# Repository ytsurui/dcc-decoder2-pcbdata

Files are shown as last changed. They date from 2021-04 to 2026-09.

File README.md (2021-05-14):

# ATtiny1606 DCC Decoder PCB Data

NMRA規格の信号を受信して動作する、DCCデコーダの基板設計データです。

主にNゲージ鉄道模型への搭載を想定して小型に設計しております。

## すべての基板に共通するスペック
  * 走行用モーター出力
  * BEMF読み取りによるフィードバック制御に対応
  * 最大7ファンクション出力
  * BiDi (Railcom) 出力
  * (試験的実装) Asymmetric DCCの認識回路
  
くわしくは、各基板のデータをご覧ください。
  * [K3066RA](docs/readme-K3066.md)
  * [K3057RA](docs/readme-K3057.md)
  * [M02F7RA Roomlight-N](docs/readme-roomlight-n.md)
  * [M02F7RA](docs/readme-normal.md)

## 閲覧・編集に必要なCAD (開発環境)
  * KiCad Version (5.1.9)-1 (またはそれ以降)

## 回路図

  * [v2021-04](https://github.com/ytsurui/dcc-decoder2-pcbdata/releases/tag/v2021-04)

## 対応するファームウェア
  * [ATtiny1606 DCC Decoder Firmware](https://github.com/ytsurui/dcc-decoder2-firmware)

このリポジトリに含まれる、すべての種類のデコーダが上記のファームウェアで動くように設計されています。

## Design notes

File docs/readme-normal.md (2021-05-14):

# ATtiny1606 DCC Decoder PCB Data (M02F7RA)

NMRA規格の信号を受信して動作する、DCCデコーダの基板設計データです。

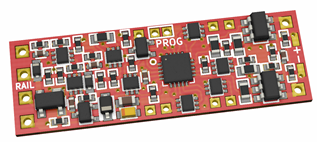
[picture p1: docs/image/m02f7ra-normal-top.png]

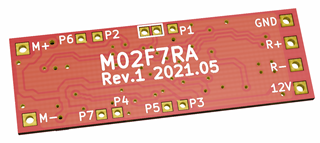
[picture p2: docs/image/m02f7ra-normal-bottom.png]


30mm x 10mmの汎用形状となっており、基板搭載スペースが確保可能な鉄道模型車両に搭載することができます。

  * [基板設計データ](../Normal/KiCad)
  
## 主要スペック
  * 組み立て後の基板サイズ： 30mm x 10mm x 1.7mm
  * 推奨最大電圧: 16V (搭載する鉄道模型車両の最大電圧以下で使用してください)
  * 出力電流: 最大0.5A (モーター) / 0.1A (ファンクション)
  * コンデンサの搭載や、室内灯電源に対応する+12V / GNDのランドを用意
  * マイコン書き込み用端子を用意し、実装後のプログラム書き換えも可能<br>UPDI 2pin Interface (GND / UPDI)

## 主な機能
  * モーター制御回路 (BEMF読み取り回路付き)
  * ファンクション出力 x 7<br>P1-P7すべてMOSFETによるドライブ、電流制限なし
  * BiDi (Railcom) 送出回路
  * (試験的実装) Asymmetric DCCの認識回路

## ファンクションの割り当て
<table>
  <tr>
    <td>基板上の番号</td>
    <td>ファンクションの推奨割り当て</td>
    <td>電気的特性</td>
  </tr>
  <tr>
    <td>P1</td>
    <td>ヘッドライト (前進)</td>
    <td>定電流出力 (約10mA)</td>
  </tr>
  <tr>
    <td>P2</td>
    <td>テールライト左 (後進/入替灯)</td>
    <td>定電流出力 (約1mA)</td>
  </tr>
  <tr>
    <td>P3</td>
    <td>テールライト右 (後進)</td>
    <td>定電流出力 (約1mA、スルーホール)<br>定電流出力 (約10mA、裏面パッド)</td>
  </tr>
  <tr>
    <td>P4</td>
    <td>ヘッドライト (後進)</td>
    <td>定電流出力 (約10mA)</td>
  </tr>
  <tr>
    <td>P5</td>
    <td>テールライト左 (前進/入替灯)</td>
    <td>定電流出力 (約1mA)</td>
  </tr>
  <tr>
    <td>P6</td>
    <td>テールライト右 (前進)</td>
    <td>定電流出力 (約1mA、スルーホール)<br>定電流出力 (約10mA、裏面パッド)</td>
  </tr>
  <tr>
    <td>P7</td>
    <td>キャブライト等、汎用ファンクション</td>
    <td>オープンドレイン (Max50mA程度)</td>
  </tr>
</table>

※番号表記はすべて基板の裏面にあります。

※ファンクションの推奨割り当ては対応するファームウェアでの初期状態を示しているものであり、ファームウェアを改修したり設定を変更すると変化する場合があります。

## 閲覧・編集に必要なCAD (開発環境)
  * KiCad Version (5.1.9)-1 (またはそれ以降)

### 対応するファームウェア
  * [ATtiny1606 DCC Decoder Firmware](https://github.com/ytsurui/dcc-decoder2-firmware)

### 各種ドキュメント
  * [パーツリスト](partslist-normal.md)

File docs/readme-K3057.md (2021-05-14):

# ATtiny1606 DCC Decoder PCB Data for KATO 3057 PCB Board

NMRA規格の信号を受信して動作する、DCCデコーダの基板設計データです。

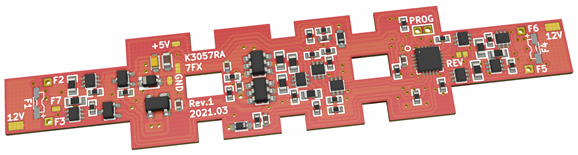
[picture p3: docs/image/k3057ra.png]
PCB 3D Preview


KATO製鉄道模型に搭載されている、3057と刻印のある基板と交換して取り付けができます。
<br>(その他、3010や3023など、形状が同等である他の刻印の基板との交換にも対応できる場合があります。)

  * [基板設計データ](../K3057/KiCad)
  * [面付けデータ](../K3057/KiCad-Panelized)
  * [ガーバーデータ(面付け済)](../K3057/Gerber-Panelized)
  * [メタルマスクデータ(面付け済)](../K3057/Stencil-Panelized)
  
面付け済みのデータについては、elecrowにて製造できることを確認済みです。

## 主要スペック
  * 組み立て後の基板サイズ： 69mm x 14mm x 1.7mm
  * 推奨最大電圧: 16V (搭載する鉄道模型車両の最大電圧以下で使用してください)
  * 出力電流: 最大0.5A (モーター) / 0.1A (ファンクション)
  * コンデンサの搭載や、室内灯電源に対応する+12V / GNDのランドを用意
  * マイコン書き込み用端子を用意し、実装後のプログラム書き換えも可能<br>UPDI 2pin Interface (GND / UPDI)

## 主な機能
  * モーター制御回路 (BEMF読み取り回路付き)
  * ファンクション出力 x 7<br>P1-P6は定電流出力、P7は電流制限なし
  * BiDi (Railcom) 送出回路
  * (試験的実装) Asymmetric DCCの認識回路

## ファンクションの割り当て
<table>
  <tr>
    <td>基板上の番号</td>
    <td>ファンクションの推奨割り当て</td>
    <td>電気的特性</td>
  </tr>
  <tr>
    <td>P1</td>
    <td>ヘッドライト (前進)</td>
    <td>定電流出力 (約10mA)</td>
  </tr>
  <tr>
    <td>P2</td>
    <td>テールライト左 (後進/入替灯)</td>
    <td>定電流出力 (約1mA)</td>
  </tr>
  <tr>
    <td>P3</td>
    <td>テールライト右 (後進)</td>
    <td>定電流出力 (約1mA、スルーホール)<br>定電流出力 (約10mA、裏面パッド)</td>
  </tr>
  <tr>
    <td>P4</td>
    <td>ヘッドライト (後進)</td>
    <td>定電流出力 (約10mA)</td>
  </tr>
  <tr>
    <td>P5</td>
    <td>テールライト左 (前進/入替灯)</td>
    <td>定電流出力 (約1mA)</td>
  </tr>
  <tr>
    <td>P6</td>
    <td>テールライト右 (前進)</td>
    <td>定電流出力 (約1mA、スルーホール)<br>定電流出力 (約10mA、裏面パッド)</td>
  </tr>
  <tr>
    <td>P7</td>
    <td>キャブライト等、汎用ファンクション</td>
    <td>オープンドレイン (Max50mA程度)</td>
  </tr>
</table>

※ファンクションの推奨割り当ては対応するファームウェアでの初期状態を示しているものであり、ファームウェアを改修したり設定を変更すると変化する場合があります。

## 閲覧・編集に必要なCAD (開発環境)
  * KiCad Version (5.1.9)-1 (またはそれ以降)

### 対応するファームウェア
  * [ATtiny1606 DCC Decoder Firmware](https://github.com/ytsurui/dcc-decoder2-firmware)

### 各種ドキュメント
  * [パーツリスト](partslist-K3057.md)

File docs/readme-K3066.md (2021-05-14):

# ATtiny1606 DCC Decoder PCB Data for KATO 3066 PCB Board

NMRA規格の信号を受信して動作する、DCCデコーダの基板設計データです。

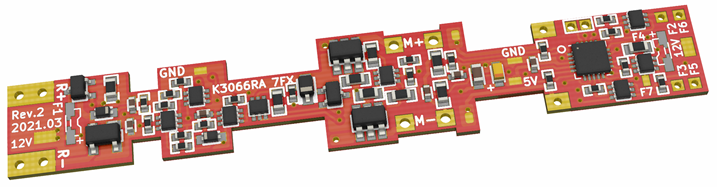
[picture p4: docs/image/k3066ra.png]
PCB 3D Preview


KATO製鉄道模型に搭載されている、3066と刻印のある基板と交換して取り付けができます。
<br>(その他、3070など、形状が同等である他の刻印の基板との交換にも対応できる場合があります。)

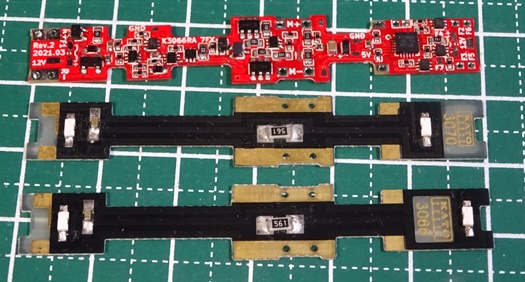
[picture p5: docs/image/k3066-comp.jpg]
PCB Compare


  * [基板設計データ](../K3066/KiCad)
  * [面付けデータ](../K3066/KiCad-Panelized)
  * [ガーバーデータ(面付け済)](../K3066/Gerber-Panelized)
  * [メタルマスクデータ(面付け済)](../K3066/Stencil-Panelized)
  
面付け済みのデータについては、elecrowにて製造できることを確認済みです。

## 主要スペック
  * 組み立て後の基板サイズ： 60mm x 10.5mm x 1.7mm
  * 推奨最大電圧: 16V (搭載する鉄道模型車両の最大電圧以下で使用してください)
  * 出力電流: 最大0.5A (モーター) / 0.1A (ファンクション)
  * コンデンサの搭載や、室内灯電源に対応する+12V / GNDのランドを用意
  * マイコン書き込み用端子を用意し、実装後のプログラム書き換えも可能<br>UPDI 2pin Interface (GND / UPDI)

## 主な機能
  * モーター制御回路 (BEMF読み取り回路付き)
  * ファンクション出力 x 7<br>P1-P6は定電流出力、P7は電流制限なし
  * BiDi (Railcom) 送出回路
  * (試験的実装) Asymmetric DCCの認識回路

## ファンクションの割り当て
<table>
  <tr>
    <td>基板上の番号</td>
    <td>ファンクションの推奨割り当て</td>
    <td>電気的特性</td>
  </tr>
  <tr>
    <td>P1</td>
    <td>ヘッドライト (前進)</td>
    <td>定電流出力 (約10mA)</td>
  </tr>
  <tr>
    <td>P2</td>
    <td>テールライト左 (後進/入替灯)</td>
    <td>定電流出力 (約1mA)</td>
  </tr>
  <tr>
    <td>P3</td>
    <td>テールライト右 (後進)</td>
    <td>定電流出力 (約1mA)</td>
  </tr>
  <tr>
    <td>P4</td>
    <td>ヘッドライト (後進)</td>
    <td>定電流出力 (約10mA)</td>
  </tr>
  <tr>
    <td>P5</td>
    <td>テールライト左 (前進/入替灯)</td>
    <td>定電流出力 (約1mA)</td>
  </tr>
  <tr>
    <td>P6</td>
    <td>テールライト右 (前進)</td>
    <td>定電流出力 (約1mA)</td>
  </tr>
  <tr>
    <td>P7</td>
    <td>キャブライト等、汎用ファンクション</td>
    <td>オープンドレイン (Max50mA程度)</td>
  </tr>
</table>

※ファンクションの推奨割り当ては対応するファームウェアでの初期状態を示しているものであり、ファームウェアを改修したり設定を変更すると変化する場合があります。

## 閲覧・編集に必要なCAD (開発環境)
  * KiCad Version (5.1.9)-1 (またはそれ以降)

## 対応するファームウェア
  * [ATtiny1606 DCC Decoder Firmware](https://github.com/ytsurui/dcc-decoder2-firmware)

## 各種ドキュメント
  * [パーツリスト](partslist-K3066.md)

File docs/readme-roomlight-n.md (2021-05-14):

# ATtiny1606 DCC Decoder PCB Data for Roomlight (Narrow Type)

NMRA規格の信号を受信して動作する、DCCデコーダの基板設計データです。

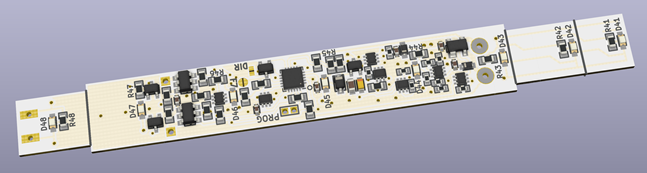
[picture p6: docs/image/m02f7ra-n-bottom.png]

PCB 3D Preview

TOMIX製やマイクロエース製の室内灯に近い形としており、室内灯一体型デコーダとしての利用が可能です。

  * [基板設計データ](../RoomLightNarrow/KiCad)
  * [面付けデータ](../RoomLightNarrow/KiCad-Panelized)
  * [ガーバーデータ(面付け済)](../RoomLightNarrow/Gerber-Panelized)
  * [メタルマスクデータ(面付け済)](../RoomLightNarrow/Stencil-Panelized)
  
面付け済みのデータについては、elecrowにて製造できることを確認済みです。

## 主要スペック
  * 組み立て後の基板サイズ： 87mm x 10mm x 1.7mm
  * 推奨最大電圧: 16V (搭載する鉄道模型車両の最大電圧以下で使用してください)
  * 出力電流: 最大0.5A (モーター) / 0.1A (ファンクション)
  * コンデンサの搭載や、室内灯電源に対応する+12V / GNDのランドを用意
  * マイコン書き込み用端子を用意し、実装後のプログラム書き換えも可能<br>UPDI 2pin Interface (GND / UPDI)

## 主な機能
  * モーター制御回路 (BEMF読み取り回路付き)
  * ファンクション出力 x 7<br>P1-P6はパッドで用意、P7は室内灯LED駆動回路に直結<br>※すべてのパッドで電流制限回路なし
  * BiDi (Railcom) 送出回路
  * (試験的実装) Asymmetric DCCの認識回路

## ファンクションの割り当て
<table>
  <tr>
    <td>基板上の番号</td>
    <td>ファンクションの推奨割り当て</td>
    <td>電気的特性</td>
  </tr>
  <tr>
    <td>P1</td>
    <td>ヘッドライト (前進)</td>
    <td>オープンドレイン (Max50mA程度)</td>
  </tr>
  <tr>
    <td>P2</td>
    <td>テールライト左 (後進/入替灯)</td>
    <td>オープンドレイン (Max50mA程度)</td>
  </tr>
  <tr>
    <td>P3</td>
    <td>テールライト右 (後進)</td>
    <td>オープンドレイン (Max50mA程度)</td>
  </tr>
  <tr>
    <td>P4</td>
    <td>ヘッドライト (後進)</td>
    <td>オープンドレイン (Max50mA程度)</td>
  </tr>
  <tr>
    <td>P5</td>
    <td>テールライト左 (前進/入替灯)</td>
    <td>オープンドレイン (Max50mA程度)</td>
  </tr>
  <tr>
    <td>P6</td>
    <td>テールライト右 (前進)</td>
    <td>オープンドレイン (Max50mA程度)</td>
  </tr>
  <tr>
    <td>P7</td>
    <td>キャブライト等、汎用ファンクション</td>
    <td>室内灯回路直結 (Max50mA程度)</td>
  </tr>
  <tr>
    <td>MOTOR+ / MOTOR-<br>(モータードライバ)</td>
    <td>ヘッドライト / テールライト<br>(ライト基板を無改造で接続)</td>
    <td>Hブリッジ出力</td>
  </tr>
</table>

モータードライバをファンクションとして利用するためには、CV値を書き換える必要がある場合があります。
<br>また、走行用モーター出力とは排他利用となります。

※ファンクションの推奨割り当ては対応するファームウェアでの初期状態を示しているものであり、ファームウェアを改修したり設定を変更すると変化する場合があります。

## 閲覧・編集に必要なCAD (開発環境)
  * KiCad Version (5.1.9)-1 (またはそれ以降)

### 対応するファームウェア
  * [ATtiny1606 DCC Decoder Firmware](https://github.com/ytsurui/dcc-decoder2-firmware)

### 各種ドキュメント
  * [パーツリスト](partslist-RoomlightNarrow.md)

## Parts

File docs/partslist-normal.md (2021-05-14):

# Parts List (MotorDecoder2-Normal, Rev1)

<table>
  <th>
    <td>Name</td>
    <td>Package</td>
    <td>Count</td>
    <td>Shop Links</td>
  </th>
  <tr>
    <td>U2</td>
    <td>ATtiny1606-MNR</td>
    <td>VQFN-20 (3x3mm)</td>
    <td>1</td>
    <td><a href="https://www.digikey.jp/product-detail/ja/microchip-technology/ATTINY1606-MNR/150-ATTINY1606-MNRCT-ND/11476321">Digikey (ja)</a></td>
  </tr>
  <tr>
    <td>D1</td>
    <td>BAS3007A-RPP</td>
    <td>SOT-143</td>
    <td>1</td>
    <td><a href="https://www.digikey.jp/product-detail/ja/infineon-technologies/BAS3007ARPPE6327HTSA1/BAS3007ARPPE6327HTSA1CT-ND/2023144">Digikey (ja)</a><br />
    <a href="https://www.digikey.jp/product-detail/en/infineon-technologies/BAS3007ARPPE6327HTSA1/BAS3007ARPPE6327HTSA1CT-ND/2023144">Digikey (en)</a></td>
  </tr>
  <tr>
    <td>D3</td>
    <td>UDZV5.6B</td>
    <td>SOD-323</td>
    <td>1</td>
    <td><a href="https://www.digikey.jp/product-detail/ja/rohm-semiconductor/UDZVTE-175-1B/UDZVTE-175-1BCT-ND/4571455">Digikey (ja)</a><br />
    <a href="https://www.digikey.jp/product-detail/en/rohm-semiconductor/UDZVTE-175-1B/UDZVTE-175-1BCT-ND/4571455">Digikey (en)</a></td>
  </tr>
  <tr>
    <td>D11, D12</td>
    <td>LED</td>
    <td></td>
    <td>2</td>
    <td></td>
  </tr>
  <tr>
    <td>D21, D22</td>
    <td>BAT43XV2</td>
    <td></td>
    <td>2</td>
    <td></td>
  </tr>
  <tr>
    <td>Q1, Q2</td>
    <td>DMG6601LVT<br>DMG6602SVTQ<br>FDC6333</td>
    <td>SOT-23-6</td>
    <td>2</td>
    <td><a href="https://www.digikey.jp/product-detail/ja/diodes-incorporated/DMG6601LVT-7/DMG6601LVT-7DICT-ND/3677910">Digikey, DMG6601LVT (ja)</a><br />
    <a href="https://www.digikey.jp/product-detail/en/diodes-incorporated/DMG6601LVT-7/DMG6601LVT-7DICT-ND/3677910">Digikey, DMG6601LVT (en)</a><br>
    <a href="https://www.digikey.jp/product-detail/ja/diodes-incorporated/DMG6602SVTQ-7/DMG6602SVTQ-7DICT-ND/5176059">Digikey, DMG6602SVTQ (ja)</a><br>
    <a href="https://www.digikey.jp/product-detail/en/diodes-incorporated/DMG6602SVTQ-7/DMG6602SVTQ-7DICT-ND/5176059">Digikey, DMG6602SVTQ (en)</a><br>
    <a href="https://www.digikey.jp/product-detail/ja/on-semiconductor/FDC6333C/FDC6333CCT-ND/965584">Digikey, FDC6333 (ja)</a><br>
    <a href="https://www.digikey.jp/product-detail/en/on-semiconductor/FDC6333C/FDC6333CCT-ND/965584">Digikey, FDC6333 (en)</a>
    </td>
  </tr>
  <tr>
    <td>Q3, Q8</td>
    <td>PMBT3904VS,115</td>
    <td>SOT-666</td>
    <td>2</td>
    <td><a href="https://www.digikey.jp/product-detail/ja/nexperia-usa-inc/PMBT3904VS,115/1727-5177-1-ND/2531775">Digikey (ja)</a></td>
  </tr>
  <tr>
    <td>Q5</td>
    <td>2SC4116-GR</td>
    <td>SC-70</td>
    <td>1</td>
    <td><a href="https://www.digikey.jp/product-detail/ja/toshiba-semiconductor-and-storage/2SC4116-GR-LF/2SC4116-GRLFCT-ND/3191333">Digikey (ja)</a><br />
    <a href="https://www.digikey.jp/product-detail/en/toshiba-semiconductor-and-storage/2SC4116-GR-LF/2SC4116-GRLFCT-ND/3191333">Digikey (en)</a><br />
    <a href="https://akizukidenshi.com/catalog/g/gI-02705/">秋月電子通商</a></td>
  </tr>
  <tr>
    <td>Q6, Q21</td>
    <td>PMBT3906VS,115</td>
    <td>SOT-666</td>
    <td>2</td>
    <td><a href="https://www.digikey.jp/product-detail/ja/nexperia-usa-inc/PMBT3906VS,115/1727-5179-1-ND/2531777">Digikey (ja)</a></td>
  </tr>
  <tr>
    <td>Q12-Q14, Q22</td>
    <td>SSM6N7002BFE</td>
    <td>SOT-666</td>
    <td>5</td>
    <td><a href="https://www.digikey.jp/product-detail/ja/toshiba-semiconductor-and-storage/SSM6N7002BFE,LM/SSM6N7002BFELMCT-ND/4880063">Digikey (ja)</a></td>
  </tr>
  <tr>
    <td>Q11</td>
    <td>SSM3K7002BFU<br>SSM3K7002KFU</td>
    <td>SC-70</td>
    <td>1</td>
    <td><a href="https://www.digikey.jp/product-detail/ja/toshiba-semiconductor-and-storage/SSM3K7002KFU-LF/SSM3K7002KFULFCT-ND/8543465">Digikey (ja)</a><br><a href="https://akizukidenshi.com/catalog/g/gI-08576/">秋月電子通商</a></td>
  </tr>
  <tr>
    <td>C1, C5</td>
	  <td>0.1uF 25V 1005</td>
	  <td>1.0mm x 0.5mm</td>
	  <td>2</td>
    <td><a href="https://www.digikey.jp/product-detail/ja/murata-electronics/GRM155R71H104KE14J/490-13342-1-ND/5973352">Digikey (ja)</a><br />
    <a href="https://www.digikey.jp/product-detail/en/murata-electronics/GRM155R71H104KE14J/490-13342-1-ND/5973352">Digikey (en)</a><br />
    <a href="https://akizukidenshi.com/catalog/g/gP-13377/">秋月電子通商</a></td>
  </tr>
  <tr>
    <td>C3</td>
    <td>22uF 6.3V 1608</td>
    <td>1.6mm x 0.8mm</td>
    <td>1</td>
    <td><a href="https://www.digikey.jp/product-detail/ja/murata-electronics/GRM188R60J226MEA0D/490-7611-1-ND/4280544">Digikey (ja)</a><br />
    <a href="https://www.digikey.jp/product-detail/en/murata-electronics/GRM188R60J226MEA0D/490-7611-1-ND/4280544">Digikey (en)</a><br />
    <a href="https://akizukidenshi.com/catalog/g/gP-08062/">秋月電子通商</a></td>
  </tr>
  <tr>
    <td>C4</td>
    <td>47uF 6.3V 1608 Tantalum</td>
    <td>1.6mm x 0.8mm</td>
    <td>1</td>
    <td><a href="https://www.digikey.jp/product-detail/ja/rohm-semiconductor/TCSOM0J476M8R-ZM1/511-11830-1-ND/10258991">Digikey (ja)</a></td>
  </tr>
  <tr>
    <td>C7</td>
    <td>1800pF 50V 1005</td>
    <td>1.0x0.5mm</td>
    <td>1</td>
    <td><a href="https://akizukidenshi.com/catalog/g/gP-15443/">秋月電子通商</a></td>
  </tr>
  <tr>
    <td>C11, C12</td>
	<td>1.0uF 25V 1005</td>
	<td>1.0mm x 0.5mm</td>
	<td>2</td>
    <td><a href="https://www.digikey.jp/product-detail/ja/murata-electronics/GRM155R71H104KE14J/490-13342-1-ND/5973352">Digikey (ja)</a><br />
    <a href="https://www.digikey.jp/product-detail/en/murata-electronics/GRM155R71H104KE14J/490-13342-1-ND/5973352">Digikey (en)</a><br />
    <a href="https://akizukidenshi.com/catalog/g/gP-13377/">秋月電子通商</a></td>
  </tr>
  <tr>
    <td>R1, R2, R17, R18</td>
    <td>100kohm 1/16W 1005</td>
    <td>1.0x0.5mm</td>
    <td>4</td>
    <td><a href="https://www.digikey.jp/product-detail/ja/bourns-inc/CR0402-FX-1003GLF/CR0402-FX-1003GLFCT-ND/3740841">Digikey (ja)</a></td>
  </tr>
  <tr>
    <td>R3, R4</td>
    <td>1kohm 1/10W 1608</td>
    <td>1.6x0.8mm</td>
    <td>2</td>
    <td><a href="https://www.digikey.jp/products/ja/resistors/chip-resistor-surface-mount/52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">Digikey (ja)</a><br />
    <a href="https://www.digikey.jp/products/en/resistors/chip-resistor-surface-mount/52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">Digikey (en)</a><br />
    <a href="https://akizukidenshi.com/catalog/g/gR-14122/">秋月電子通商</a></td>
  </tr>
  <tr>
    <td>R5, R6</td>
    <td>330ohm 1/10W 1608</td>
    <td>1.6x0.8mm</td>
    <td>2</td>
    <td><a href="https://www.digikey.jp/products/ja/resistors/chip-resistor-surface-mount/52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">Digikey (ja)</a><br />
    <a href="https://www.digikey.jp/products/en/resistors/chip-resistor-surface-mount/52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">Digikey (en)</a><br />
    <a href="https://akizukidenshi.com/catalog/g/gR-06331/">秋月電子通商</a></td>
  </tr>
  <tr>
    <td>R7, R8, R11, R31, R35</td>
    <td>1kohm 1/16W 1005</td>
    <td>1.0x0.5mm</td>
    <td>5</td>
    <td><a href="https://www.digikey.jp/products/ja/resistors/chip-resistor-surface-mount/52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">Digikey (ja)</a></td>
  </tr>
  <tr>
    <td>R12, R33, R37</td>
    <td>4.7kohm 1/16W 1005</td>
    <td>1.0x0.5mm</td>
    <td>3</td>
    <td><a href="https://www.digikey.jp/product-detail/ja/koa-speer-electronics-inc/RK73B1ETTP472J/2019-RK73B1ETTP472JCT-ND/9846006">Digikey (ja)</a></td>
  </tr>
  <tr>
    <td>R9, R10, R13, R16, R32, R34, R36, R38</td>
    <td>10kohm 1/16W 1005</td>
    <td>1.0x0.5mm</td>
    <td>8</td>
    <td><a href="https://www.digikey.jp/product-detail/ja/koa-speer-electronics-inc/RK73B1ETTP103J/2019-RK73B1ETTP103JCT-ND/9846004">Digikey (ja)</a></td>
  </tr>
  <tr>
    <td>R14</td>
    <td>22ohm 1/10W 1608</td>
    <td>1.6x0.8mm</td>
    <td>1</td>
    <td><a href="https://www.digikey.jp/product-detail/ja/koa-speer-electronics-inc/RK73B1JTTD220J/2019-RK73B1JTTD220JCT-ND/9846752">Digikey (ja)</a></td>
  </tr>
  <tr>
    <td>R15</td>
    <td>6.8kohm 1/16W 1005</td>
    <td>1.0x0.5mm</td>
    <td>1</td>
    <td><a href="https://www.digikey.jp/product-detail/ja/koa-speer-electronics-inc/RK73B1ETTP682J/2019-RK73B1ETTP682JCT-ND/9846058">Digikey (ja)</a></td>
  </tr>

</table>

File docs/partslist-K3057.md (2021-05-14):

# Parts List (MotorDecoder2-K3057, Rev2)

<table>
  <th>
    <td>Name</td>
    <td>Package</td>
    <td>Count</td>
    <td>Shop Links</td>
  </th>
  <tr>
    <td>U2</td>
    <td>ATtiny1606-MNR</td>
    <td>VQFN-20 (3x3mm)</td>
    <td>1</td>
    <td><a href="https://www.digikey.jp/product-detail/ja/microchip-technology/ATTINY1606-MNR/150-ATTINY1606-MNRCT-ND/11476321">Digikey (ja)</a></td>
  </tr>
  <tr>
    <td>D1</td>
    <td>BAS3007A-RPP</td>
    <td>SOT-143</td>
    <td>1</td>
    <td><a href="https://www.digikey.jp/product-detail/ja/infineon-technologies/BAS3007ARPPE6327HTSA1/BAS3007ARPPE6327HTSA1CT-ND/2023144">Digikey (ja)</a><br />
    <a href="https://www.digikey.jp/product-detail/en/infineon-technologies/BAS3007ARPPE6327HTSA1/BAS3007ARPPE6327HTSA1CT-ND/2023144">Digikey (en)</a></td>
  </tr>
  <tr>
    <td>D3</td>
    <td>UDZV5.6B</td>
    <td>SOD-323</td>
    <td>1</td>
    <td><a href="https://www.digikey.jp/product-detail/ja/rohm-semiconductor/UDZVTE-175-1B/UDZVTE-175-1BCT-ND/4571455">Digikey (ja)</a><br />
    <a href="https://www.digikey.jp/product-detail/en/rohm-semiconductor/UDZVTE-175-1B/UDZVTE-175-1BCT-ND/4571455">Digikey (en)</a></td>
  </tr>
  <tr>
    <td>D11, D12</td>
    <td>LED</td>
    <td></td>
    <td>2</td>
    <td></td>
  </tr>
  <tr>
    <td>D21, D22</td>
    <td>BAT43XV2</td>
    <td></td>
    <td>2</td>
    <td></td>
  </tr>
  <tr>
    <td>Q1, Q2</td>
    <td>DMG6601LVT<br>DMG6602SVTQ<br>FDC6333</td>
    <td>SOT-23-6</td>
    <td>2</td>
    <td><a href="https://www.digikey.jp/product-detail/ja/diodes-incorporated/DMG6601LVT-7/DMG6601LVT-7DICT-ND/3677910">Digikey, DMG6601LVT (ja)</a><br />
    <a href="https://www.digikey.jp/product-detail/en/diodes-incorporated/DMG6601LVT-7/DMG6601LVT-7DICT-ND/3677910">Digikey, DMG6601LVT (en)</a><br>
    <a href="https://www.digikey.jp/product-detail/ja/diodes-incorporated/DMG6602SVTQ-7/DMG6602SVTQ-7DICT-ND/5176059">Digikey, DMG6602SVTQ (ja)</a><br>
    <a href="https://www.digikey.jp/product-detail/en/diodes-incorporated/DMG6602SVTQ-7/DMG6602SVTQ-7DICT-ND/5176059">Digikey, DMG6602SVTQ (en)</a><br>
    <a href="https://www.digikey.jp/product-detail/ja/on-semiconductor/FDC6333C/FDC6333CCT-ND/965584">Digikey, FDC6333 (ja)</a><br>
    <a href="https://www.digikey.jp/product-detail/en/on-semiconductor/FDC6333C/FDC6333CCT-ND/965584">Digikey, FDC6333 (en)</a>
    </td>
  </tr>
  <tr>
    <td>Q3, Q8</td>
    <td>PMBT3904VS,115</td>
    <td>SOT-666</td>
    <td>2</td>
    <td><a href="https://www.digikey.jp/product-detail/ja/nexperia-usa-inc/PMBT3904VS,115/1727-5177-1-ND/2531775">Digikey (ja)</a></td>
  </tr>
  <tr>
    <td>Q5</td>
    <td>2SC4116-GR</td>
    <td>SC-70</td>
    <td>1</td>
    <td><a href="https://www.digikey.jp/product-detail/ja/toshiba-semiconductor-and-storage/2SC4116-GR-LF/2SC4116-GRLFCT-ND/3191333">Digikey (ja)</a><br />
    <a href="https://www.digikey.jp/product-detail/en/toshiba-semiconductor-and-storage/2SC4116-GR-LF/2SC4116-GRLFCT-ND/3191333">Digikey (en)</a><br />
    <a href="https://akizukidenshi.com/catalog/g/gI-02705/">秋月電子通商</a></td>
  </tr>
  <tr>
    <td>Q6, Q21</td>
    <td>PMBT3906VS,115</td>
    <td>SOT-666</td>
    <td>2</td>
    <td><a href="https://www.digikey.jp/product-detail/ja/nexperia-usa-inc/PMBT3906VS,115/1727-5179-1-ND/2531777">Digikey (ja)</a></td>
  </tr>
  <tr>
    <td>Q11-Q14, Q22</td>
    <td>SSM6N7002BFE</td>
    <td>SOT-666</td>
    <td>5</td>
    <td><a href="https://www.digikey.jp/product-detail/ja/toshiba-semiconductor-and-storage/SSM6N7002BFE,LM/SSM6N7002BFELMCT-ND/4880063">Digikey (ja)</a></td>
  </tr>
  <tr>
    <td>Q15</td>
    <td>SSM3K7002BFU<br>SSM3K7002KFU</td>
    <td>SC-70</td>
    <td>1</td>
    <td><a href="https://www.digikey.jp/product-detail/ja/toshiba-semiconductor-and-storage/SSM3K7002KFU-LF/SSM3K7002KFULFCT-ND/8543465">Digikey (ja)</a><br><a href="https://akizukidenshi.com/catalog/g/gI-08576/">秋月電子通商</a></td>
  </tr>
  <tr>
    <td>C1, C5</td>
	  <td>0.1uF 25V 1005</td>
	  <td>1.0mm x 0.5mm</td>
	  <td>2</td>
    <td><a href="https://www.digikey.jp/product-detail/ja/murata-electronics/GRM155R71H104KE14J/490-13342-1-ND/5973352">Digikey (ja)</a><br />
    <a href="https://www.digikey.jp/product-detail/en/murata-electronics/GRM155R71H104KE14J/490-13342-1-ND/5973352">Digikey (en)</a><br />
    <a href="https://akizukidenshi.com/catalog/g/gP-13377/">秋月電子通商</a></td>
  </tr>
  <tr>
    <td>C3</td>
    <td>22uF 6.3V 1608</td>
    <td>1.6mm x 0.8mm</td>
    <td>1</td>
    <td><a href="https://www.digikey.jp/product-detail/ja/murata-electronics/GRM188R60J226MEA0D/490-7611-1-ND/4280544">Digikey (ja)</a><br />
    <a href="https://www.digikey.jp/product-detail/en/murata-electronics/GRM188R60J226MEA0D/490-7611-1-ND/4280544">Digikey (en)</a><br />
    <a href="https://akizukidenshi.com/catalog/g/gP-08062/">秋月電子通商</a></td>
  </tr>
  <tr>
    <td>C4</td>
    <td>47uF 6.3V 1608 Tantalum</td>
    <td>1.6mm x 0.8mm</td>
    <td>1</td>
    <td><a href="https://www.digikey.jp/product-detail/ja/rohm-semiconductor/TCSOM0J476M8R-ZM1/511-11830-1-ND/10258991">Digikey (ja)</a></td>
  </tr>
  <tr>
    <td>C7</td>
    <td>1800pF 50V 1005</td>
    <td>1.0x0.5mm</td>
    <td>1</td>
    <td><a href="https://akizukidenshi.com/catalog/g/gP-15443/">秋月電子通商</a></td>
  </tr>
  <tr>
    <td>C11, C12</td>
	<td>1.0uF 25V 1005</td>
	<td>1.0mm x 0.5mm</td>
	<td>2</td>
    <td><a href="https://www.digikey.jp/product-detail/ja/murata-electronics/GRM155R71H104KE14J/490-13342-1-ND/5973352">Digikey (ja)</a><br />
    <a href="https://www.digikey.jp/product-detail/en/murata-electronics/GRM155R71H104KE14J/490-13342-1-ND/5973352">Digikey (en)</a><br />
    <a href="https://akizukidenshi.com/catalog/g/gP-13377/">秋月電子通商</a></td>
  </tr>
  <tr>
    <td>R1, R2, R17, R18</td>
    <td>100kohm 1/16W 1005</td>
    <td>1.0x0.5mm</td>
    <td>4</td>
    <td><a href="https://www.digikey.jp/product-detail/ja/bourns-inc/CR0402-FX-1003GLF/CR0402-FX-1003GLFCT-ND/3740841">Digikey (ja)</a></td>
  </tr>
  <tr>
    <td>R3, R4</td>
    <td>1kohm 1/10W 1608</td>
    <td>1.6x0.8mm</td>
    <td>2</td>
    <td><a href="https://www.digikey.jp/products/ja/resistors/chip-resistor-surface-mount/52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">Digikey (ja)</a><br />
    <a href="https://www.digikey.jp/products/en/resistors/chip-resistor-surface-mount/52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">Digikey (en)</a><br />
    <a href="https://akizukidenshi.com/catalog/g/gR-14122/">秋月電子通商</a></td>
  </tr>
  <tr>
    <td>R5, R6</td>
    <td>330ohm 1/10W 1608</td>
    <td>1.6x0.8mm</td>
    <td>2</td>
    <td><a href="https://www.digikey.jp/products/ja/resistors/chip-resistor-surface-mount/52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">Digikey (ja)</a><br />
    <a href="https://www.digikey.jp/products/en/resistors/chip-resistor-surface-mount/52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">Digikey (en)</a><br />
    <a href="https://akizukidenshi.com/catalog/g/gR-06331/">秋月電子通商</a></td>
  </tr>
  <tr>
    <td>R7, R8, R11, R31, R35</td>
    <td>1kohm 1/16W 1005</td>
    <td>1.0x0.5mm</td>
    <td>5</td>
    <td><a href="https://www.digikey.jp/products/ja/resistors/chip-resistor-surface-mount/52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">Digikey (ja)</a></td>
  </tr>
  <tr>
    <td>R9, R10</td>
    <td>10kohm 1/10W 1608</td>
    <td>1.6mm x 0.8mm</td>
    <td>2</td>
    <td><a href="https://www.digikey.jp/products/ja/resistors/chip-resistor-surface-mount/52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">Digikey (ja)</a><br />
    <a href="https://www.digikey.jp/products/en/resistors/chip-resistor-surface-mount/52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">Digikey (en)</a><br />
    <a href="https://akizukidenshi.com/catalog/g/gR-06103/">秋月電子通商</a></td>
  </tr>
  <tr>
    <td>R12, R23-R26, R33, R37</td>
    <td>4.7kohm 1/16W 1005</td>
    <td>1.0x0.5mm</td>
    <td>7</td>
    <td><a href="https://www.digikey.jp/product-detail/ja/koa-speer-electronics-inc/RK73B1ETTP472J/2019-RK73B1ETTP472JCT-ND/9846006">Digikey (ja)</a></td>
  </tr>
  <tr>
    <td>R13, R16, R32, R34, R36, R38</td>
    <td>10kohm 1/16W 1005</td>
    <td>1.0x0.5mm</td>
    <td>5</td>
    <td><a href="https://www.digikey.jp/product-detail/ja/koa-speer-electronics-inc/RK73B1ETTP103J/2019-RK73B1ETTP103JCT-ND/9846004">Digikey (ja)</a></td>
  </tr>
  <tr>
    <td>R14</td>
    <td>22ohm 1/10W 1608</td>
    <td>1.6x0.8mm</td>
    <td>1</td>
    <td><a href="https://www.digikey.jp/product-detail/ja/koa-speer-electronics-inc/RK73B1JTTD220J/2019-RK73B1JTTD220JCT-ND/9846752">Digikey (ja)</a></td>
  </tr>
  <tr>
    <td>R15</td>
    <td>6.8kohm 1/16W 1005</td>
    <td>1.0x0.5mm</td>
    <td>1</td>
    <td><a href="https://www.digikey.jp/product-detail/ja/koa-speer-electronics-inc/RK73B1ETTP682J/2019-RK73B1ETTP682JCT-ND/9846058">Digikey (ja)</a></td>
  </tr>
  <tr>
    <td>R21, R22, R27, R28</td>
    <td>150ohm 1/10W 1608</td>
    <td>1.6x0.8mm</td>
    <td>2</td>
    <td><a href="https://www.digikey.jp/products/ja/resistors/chip-resistor-surface-mount/52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">Digikey (ja)</a></td>
  </tr>

</table>

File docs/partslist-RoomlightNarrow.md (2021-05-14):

# Parts List (MotorDecoder2-Roomlight-Narrow, Rev2)

<table>
  <th>
    <td>Name</td>
    <td>Package</td>
    <td>Count</td>
    <td>Shop Links</td>
  </th>
  <tr>
    <td>U2</td>
    <td>ATtiny1606-MNR</td>
    <td>VQFN-20 (3x3mm)</td>
    <td>1</td>
    <td><a href="https://www.digikey.jp/product-detail/ja/microchip-technology/ATTINY1606-MNR/150-ATTINY1606-MNRCT-ND/11476321">Digikey (ja)</a></td>
  </tr>
  <tr>
    <td>D1</td>
    <td>BAS3007A-RPP</td>
    <td>SOT-143</td>
    <td>1</td>
    <td><a href="https://www.digikey.jp/product-detail/ja/infineon-technologies/BAS3007ARPPE6327HTSA1/BAS3007ARPPE6327HTSA1CT-ND/2023144">Digikey (ja)</a><br />
    <a href="https://www.digikey.jp/product-detail/en/infineon-technologies/BAS3007ARPPE6327HTSA1/BAS3007ARPPE6327HTSA1CT-ND/2023144">Digikey (en)</a></td>
  </tr>
  <tr>
    <td>D3</td>
    <td>UDZV5.6B</td>
    <td>SOD-323</td>
    <td>1</td>
    <td><a href="https://www.digikey.jp/product-detail/ja/rohm-semiconductor/UDZVTE-175-1B/UDZVTE-175-1BCT-ND/4571455">Digikey (ja)</a><br />
    <a href="https://www.digikey.jp/product-detail/en/rohm-semiconductor/UDZVTE-175-1B/UDZVTE-175-1BCT-ND/4571455">Digikey (en)</a></td>
  </tr>
  <tr>
    <td>D41-D48</td>
    <td>LED 1608サイズ<br>(室内灯用)</td>
    <td>1.6mmx0.8mm</td>
    <td>8</td>
    <td>-</td>
  </tr>
  <tr>
    <td>D21, D22</td>
    <td>BAT43XV2</td>
    <td></td>
    <td>2</td>
    <td></td>
  </tr>
  <tr>
    <td>Q1, Q2</td>
    <td>DMG6601LVT<br>DMG6602SVTQ<br>FDC6333</td>
    <td>SOT-23-6</td>
    <td>2</td>
    <td><a href="https://www.digikey.jp/product-detail/ja/diodes-incorporated/DMG6601LVT-7/DMG6601LVT-7DICT-ND/3677910">Digikey, DMG6601LVT (ja)</a><br />
    <a href="https://www.digikey.jp/product-detail/en/diodes-incorporated/DMG6601LVT-7/DMG6601LVT-7DICT-ND/3677910">Digikey, DMG6601LVT (en)</a><br>
    <a href="https://www.digikey.jp/product-detail/ja/diodes-incorporated/DMG6602SVTQ-7/DMG6602SVTQ-7DICT-ND/5176059">Digikey, DMG6602SVTQ (ja)</a><br>
    <a href="https://www.digikey.jp/product-detail/en/diodes-incorporated/DMG6602SVTQ-7/DMG6602SVTQ-7DICT-ND/5176059">Digikey, DMG6602SVTQ (en)</a><br>
    <a href="https://www.digikey.jp/product-detail/ja/on-semiconductor/FDC6333C/FDC6333CCT-ND/965584">Digikey, FDC6333 (ja)</a><br>
    <a href="https://www.digikey.jp/product-detail/en/on-semiconductor/FDC6333C/FDC6333CCT-ND/965584">Digikey, FDC6333 (en)</a>
    </td>
  </tr>
  <tr>
    <td>Q3, Q8</td>
    <td>PMBT3904VS,115</td>
    <td>SOT-666</td>
    <td>2</td>
    <td><a href="https://www.digikey.jp/product-detail/ja/nexperia-usa-inc/PMBT3904VS,115/1727-5177-1-ND/2531775">Digikey (ja)</a></td>
  </tr>
  <tr>
    <td>Q5</td>
    <td>2SC4116-GR</td>
    <td>SC-70</td>
    <td>1</td>
    <td><a href="https://www.digikey.jp/product-detail/ja/toshiba-semiconductor-and-storage/2SC4116-GR-LF/2SC4116-GRLFCT-ND/3191333">Digikey (ja)</a><br />
    <a href="https://www.digikey.jp/product-detail/en/toshiba-semiconductor-and-storage/2SC4116-GR-LF/2SC4116-GRLFCT-ND/3191333">Digikey (en)</a><br />
    <a href="https://akizukidenshi.com/catalog/g/gI-02705/">秋月電子通商</a></td>
  </tr>
  <tr>
    <td>Q6, Q21</td>
    <td>PMBT3906VS,115</td>
    <td>SOT-666</td>
    <td>2</td>
    <td><a href="https://www.digikey.jp/product-detail/ja/nexperia-usa-inc/PMBT3906VS,115/1727-5179-1-ND/2531777">Digikey (ja)</a></td>
  </tr>
  <tr>
    <td>Q13, Q14, Q22</td>
    <td>SSM6N7002BFE</td>
    <td>SOT-666</td>
    <td>3</td>
    <td><a href="https://www.digikey.jp/product-detail/ja/toshiba-semiconductor-and-storage/SSM6N7002BFE,LM/SSM6N7002BFELMCT-ND/4880063">Digikey (ja)</a></td>
  </tr>
  <tr>
    <td>Q11, Q12, Q17</td>
    <td>SSM3K7002BFU<br>SSM3K7002KFU</td>
    <td>SC-70</td>
    <td>3</td>
    <td><a href="https://www.digikey.jp/product-detail/ja/toshiba-semiconductor-and-storage/SSM3K7002KFU-LF/SSM3K7002KFULFCT-ND/8543465">Digikey (ja)</a><br><a href="https://akizukidenshi.com/catalog/g/gI-08576/">秋月電子通商</a></td>
  </tr>
  <tr>
    <td>C1, C5</td>
	  <td>0.1uF 25V 1005</td>
	  <td>1.0mm x 0.5mm</td>
	  <td>2</td>
    <td><a href="https://www.digikey.jp/product-detail/ja/murata-electronics/GRM155R71H104KE14J/490-13342-1-ND/5973352">Digikey (ja)</a><br />
    <a href="https://www.digikey.jp/product-detail/en/murata-electronics/GRM155R71H104KE14J/490-13342-1-ND/5973352">Digikey (en)</a><br />
    <a href="https://akizukidenshi.com/catalog/g/gP-13377/">秋月電子通商</a></td>
  </tr>
  <tr>
    <td>C3</td>
    <td>22uF 6.3V 1608</td>
    <td>1.6mm x 0.8mm</td>
    <td>1</td>
    <td><a href="https://www.digikey.jp/product-detail/ja/murata-electronics/GRM188R60J226MEA0D/490-7611-1-ND/4280544">Digikey (ja)</a><br />
    <a href="https://www.digikey.jp/product-detail/en/murata-electronics/GRM188R60J226MEA0D/490-7611-1-ND/4280544">Digikey (en)</a><br />
    <a href="https://akizukidenshi.com/catalog/g/gP-08062/">秋月電子通商</a></td>
  </tr>
  <tr>
    <td>C4</td>
    <td>47uF 6.3V 1608 Tantalum</td>
    <td>1.6mm x 0.8mm</td>
    <td>1</td>
    <td><a href="https://www.digikey.jp/product-detail/ja/rohm-semiconductor/TCSOM0J476M8R-ZM1/511-11830-1-ND/10258991">Digikey (ja)</a></td>
  </tr>
  <tr>
    <td>C7</td>
    <td>1800pF 50V 1005</td>
    <td>1.0x0.5mm</td>
    <td>1</td>
    <td><a href="https://akizukidenshi.com/catalog/g/gP-15443/">秋月電子通商</a></td>
  </tr>
  <tr>
    <td>C11, C12</td>
	<td>1.0uF 25V 1005</td>
	<td>1.0mm x 0.5mm</td>
	<td>2</td>
    <td><a href="https://www.digikey.jp/product-detail/ja/murata-electronics/GRM155R71H104KE14J/490-13342-1-ND/5973352">Digikey (ja)</a><br />
    <a href="https://www.digikey.jp/product-detail/en/murata-electronics/GRM155R71H104KE14J/490-13342-1-ND/5973352">Digikey (en)</a><br />
    <a href="https://akizukidenshi.com/catalog/g/gP-13377/">秋月電子通商</a></td>
  </tr>
  <tr>
    <td>R1, R2, R17</td>
    <td>100kohm 1/10W 1608</td>
    <td>1.6x0.8mm</td>
    <td>3</td>
    <td><a href="https://www.digikey.jp/products/ja/resistors/chip-resistor-surface-mount/52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">Digikey (ja)</a><br />
    <a href="https://www.digikey.jp/products/en/resistors/chip-resistor-surface-mount/52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">Digikey (en)</a><br />
    <a href="https://akizukidenshi.com/catalog/g/gR-15321/">秋月電子通商</a></td>
  </tr>
  <tr>
    <td>R18</td>
    <td>100kohm 1/16W 1005</td>
    <td>1.0x0.5mm</td>
    <td>1</td>
    <td><a href="https://www.digikey.jp/product-detail/ja/bourns-inc/CR0402-FX-1003GLF/CR0402-FX-1003GLFCT-ND/3740841">Digikey (ja)</a></td>
  </tr>
  <tr>
    <td>R3, R4</td>
    <td>1kohm 1/10W 1608</td>
    <td>1.6x0.8mm</td>
    <td>2</td>
    <td><a href="https://www.digikey.jp/products/ja/resistors/chip-resistor-surface-mount/52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">Digikey (ja)</a><br />
    <a href="https://www.digikey.jp/products/en/resistors/chip-resistor-surface-mount/52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">Digikey (en)</a><br />
    <a href="https://akizukidenshi.com/catalog/g/gR-14122/">秋月電子通商</a></td>
  </tr>
  <tr>
    <td>R5, R6</td>
    <td>330ohm 1/10W 1608</td>
    <td>1.6x0.8mm</td>
    <td>2</td>
    <td><a href="https://www.digikey.jp/products/ja/resistors/chip-resistor-surface-mount/52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">Digikey (ja)</a><br />
    <a href="https://www.digikey.jp/products/en/resistors/chip-resistor-surface-mount/52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">Digikey (en)</a><br />
    <a href="https://akizukidenshi.com/catalog/g/gR-06331/">秋月電子通商</a></td>
  </tr>
  <tr>
    <td>R7, R8, R11, R31, R35</td>
    <td>1kohm 1/16W 1005</td>
    <td>1.0x0.5mm</td>
    <td>5</td>
    <td><a href="https://www.digikey.jp/products/ja/resistors/chip-resistor-surface-mount/52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">Digikey (ja)</a></td>
  </tr>
  <tr>
    <td>R9, R10</td>
    <td>10kohm 1/10W 1608</td>
    <td>1.6mm x 0.8mm</td>
    <td>2</td>
    <td><a href="https://www.digikey.jp/products/ja/resistors/chip-resistor-surface-mount/52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">Digikey (ja)</a><br />
    <a href="https://www.digikey.jp/products/en/resistors/chip-resistor-surface-mount/52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">Digikey (en)</a><br />
    <a href="https://akizukidenshi.com/catalog/g/gR-06103/">秋月電子通商</a></td>
  </tr>
  <tr>
    <td>R12<br>R41-R48</td>
    <td>4.7kohm 1/10W 1608</td>
    <td>1.6mm x 0.8mm</td>
    <td>9</td>
    <td><a href="https://www.digikey.jp/products/ja/resistors/chip-resistor-surface-mount/52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">Digikey (ja)</a><br />
    <a href="https://www.digikey.jp/products/en/resistors/chip-resistor-surface-mount/52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">Digikey (en)</a><br />
    <a href="https://akizukidenshi.com/catalog/g/gR-14121/">秋月電子通商</a></td>
  </tr>
  <tr>
    <td>R33, R37</td>
    <td>4.7kohm 1/16W 1005</td>
    <td>1.0x0.5mm</td>
    <td>2</td>
    <td><a href="https://www.digikey.jp/product-detail/ja/koa-speer-electronics-inc/RK73B1ETTP472J/2019-RK73B1ETTP472JCT-ND/9846006">Digikey (ja)</a></td>
  </tr>
  <tr>
    <td>R13, R16, R32, R34, R36, R38</td>
    <td>10kohm 1/16W 1005</td>
    <td>1.0x0.5mm</td>
    <td>5</td>
    <td><a href="https://www.digikey.jp/product-detail/ja/koa-speer-electronics-inc/RK73B1ETTP103J/2019-RK73B1ETTP103JCT-ND/9846004">Digikey (ja)</a></td>
  </tr>
  <tr>
    <td>R14</td>
    <td>22ohm 1/10W 1608</td>
    <td>1.6x0.8mm</td>
    <td>1</td>
    <td><a href="https://www.digikey.jp/product-detail/ja/koa-speer-electronics-inc/RK73B1JTTD220J/2019-RK73B1JTTD220JCT-ND/9846752">Digikey (ja)</a></td>
  </tr>
  <tr>
    <td>R15</td>
    <td>6.8kohm 1/16W 1005</td>
    <td>1.0x0.5mm</td>
    <td>1</td>
    <td><a href="https://www.digikey.jp/product-detail/ja/koa-speer-electronics-inc/RK73B1ETTP682J/2019-RK73B1ETTP682JCT-ND/9846058">Digikey (ja)</a></td>
  </tr>

</table>

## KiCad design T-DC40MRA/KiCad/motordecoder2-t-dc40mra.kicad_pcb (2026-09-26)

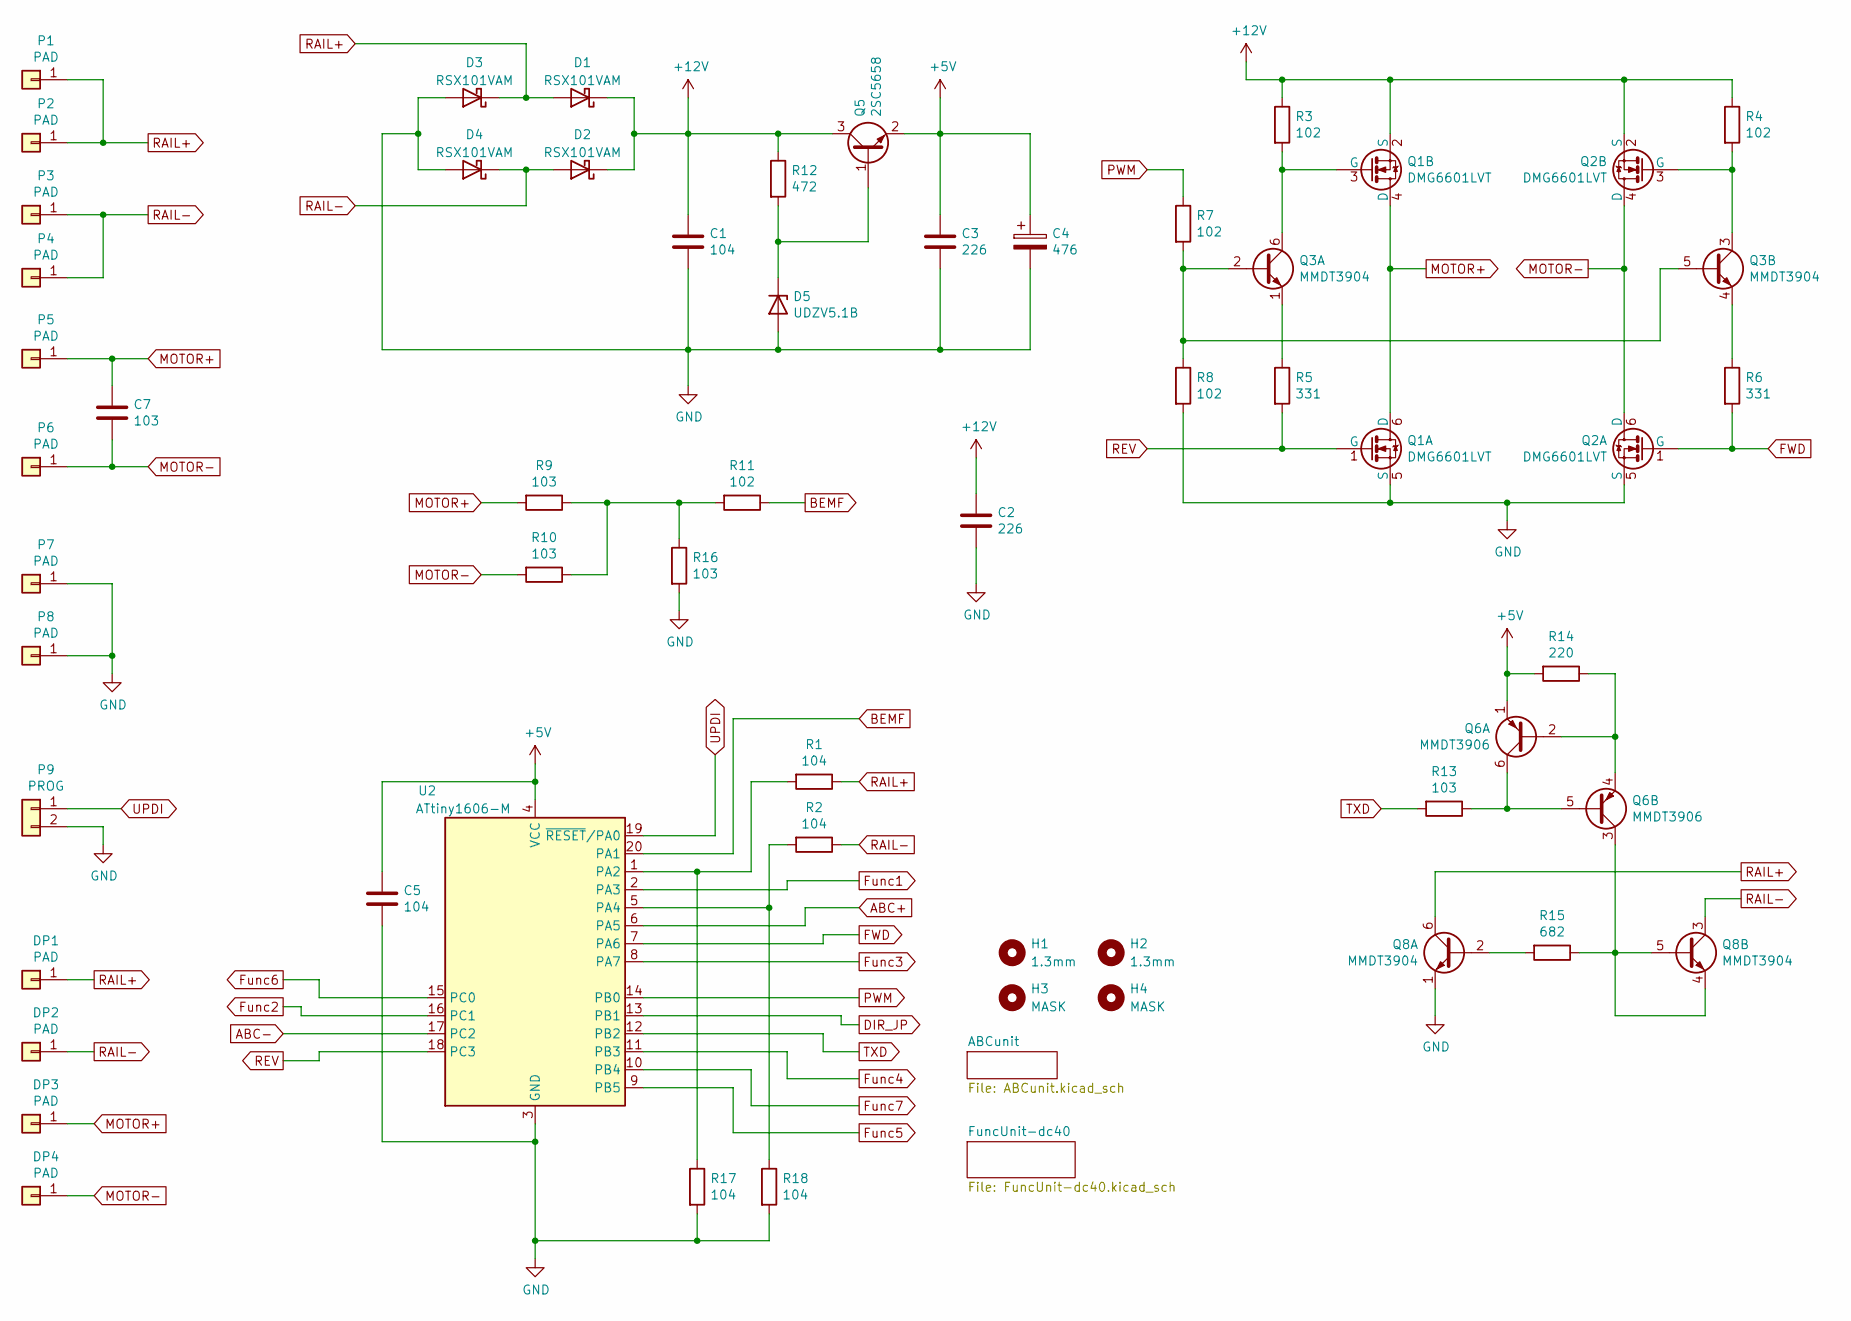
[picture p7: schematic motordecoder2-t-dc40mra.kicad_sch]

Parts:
C1, C5: 104; C_1005_v4
C2: 226; C_2012
C3: 226; C_1608
C4: 476; CP_1608
C7: 103; C_1005_v4
D1, D2, D3, D4: RSX101VAM; TUMD2M
D5: UDZV5.1B; UMD2
DP1, DP2, DP3, DP4: PAD; PAD_1.3x1.3_Hole0.9
H1, H2: 1.3mm; Hole_1.3mm
H3, H4: MASK; HOLE_MASK_LOCK
P1, P2, P3, P4: PAD; PAD_1.2x0.8_SMD
P5, P6: PAD; TOMIX_MOTORPAD_3_5sq
P7: PAD; PAD_1.0x1.8_SMD
P8: PAD; PAD_0.6x1.0_SMD
P9: PROG; PAD_PROG_2PIN_HOLE0.7
Q1, Q2: DMG6601LVT; SOT-23-6-wide
Q3, Q8: MMDT3904; SOT-666-nomark-v2
Q5: 2SC5658; SOT-723
Q6: MMDT3906; SOT-666-nomark-v2
R1, R2, R17, R18: 104; R_1005_20240411
R3, R4, R7, R8, R11: 102; R_1005_20240411
R5, R6: 331; R_1608_20240411
R9, R10, R13, R16: 103; R_1005_20240411
R12: 472; R_1005_20240411
R14: 220; R_1608_20240411
R15: 682; R_1005_20240411
U2: ATtiny1606-M; VQFN-20-1EP_3x3mm_P0.4mm_EP1.7x1.7mm

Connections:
+5V: C3.1, C4.1, C5.1, Q5.2 (E), Q6.1 (E1), R14.2, U2.4 (VCC)
+12V: C1.1, C2.1, D1.1 (K), D2.1 (K), Q1.2 (S), Q2.2 (S), Q5.3 (C), R3.1, R4.1, R12.1; also elsewhere on the board
ABC+: U2.6 (PA5); also elsewhere on the board
ABC-: U2.17 (PC2); also elsewhere on the board
BEMF: R11.1, U2.20 (PA1)
DIR_JP: U2.13 (PB1); also elsewhere on the board
FWD: Q2.1 (G), R6.2, U2.7 (PA6)
Func1: U2.2 (PA3); also elsewhere on the board
Func2: U2.16 (PC1); also elsewhere on the board
Func3: U2.8 (PA7)
Func4: U2.11 (PB3); also elsewhere on the board
Func5: U2.9 (PB5); also elsewhere on the board
Func6: U2.15 (PC0)
Func7: U2.10 (PB4); also elsewhere on the board
GND: C1.2, C2.2, C3.2, C4.2, C5.2, D3.2 (A), D4.2 (A), D5.2 (A), P7.1, P8.1, P9.2, Q1.5 (S), Q2.5 (S), Q8.1 (E1), R8.2, R16.2, R17.2, R18.2, U2.3 (GND), U2.21 (GND); also elsewhere on the board
MOTOR+: C7.1, DP3.1, P5.1, Q1.4 (D), Q1.6 (D), R9.2
MOTOR-: C7.2, DP4.1, P6.1, Q2.4 (D), Q2.6 (D), R10.2
unnamed: D5.1 (K), Q5.1 (B), R12.2
unnamed: Q1.3 (G), Q3.6 (C1), R3.2
unnamed: Q2.3 (G), Q3.3 (C2), R4.2
unnamed: Q3.2 (B1), Q3.5 (B2), R7.2, R8.1
unnamed: Q3.1 (E1), R5.1
unnamed: Q3.4 (E2), R6.1
unnamed: Q6.2 (B1), Q6.4 (E2), R14.1
unnamed: Q6.5 (B2), Q6.6 (C1), R13.1
unnamed: Q6.3 (C2), Q8.4 (E2), Q8.5 (B2), R15.1
unnamed: Q8.2 (B1), R15.2
unnamed: R9.1, R10.1, R11.2, R16.1
unnamed: R1.2, R17.1, U2.1 (PA2)
unnamed: R2.2, R18.1, U2.5 (PA4)
PWM: R7.1, U2.14 (PB0)
RAIL+: D1.2 (A), D3.1 (K), DP1.1, P1.1, P2.1, Q8.6 (C1), R1.1; also elsewhere on the board
RAIL-: D2.2 (A), D4.1 (K), DP2.1, P3.1, P4.1, Q8.3 (C2), R2.1; also elsewhere on the board
REV: Q1.1 (G), R5.2, U2.18 (PC3)
TXD: R13.2, U2.12 (PB2)
UPDI: P9.1, U2.19 (~RESET/PA0)

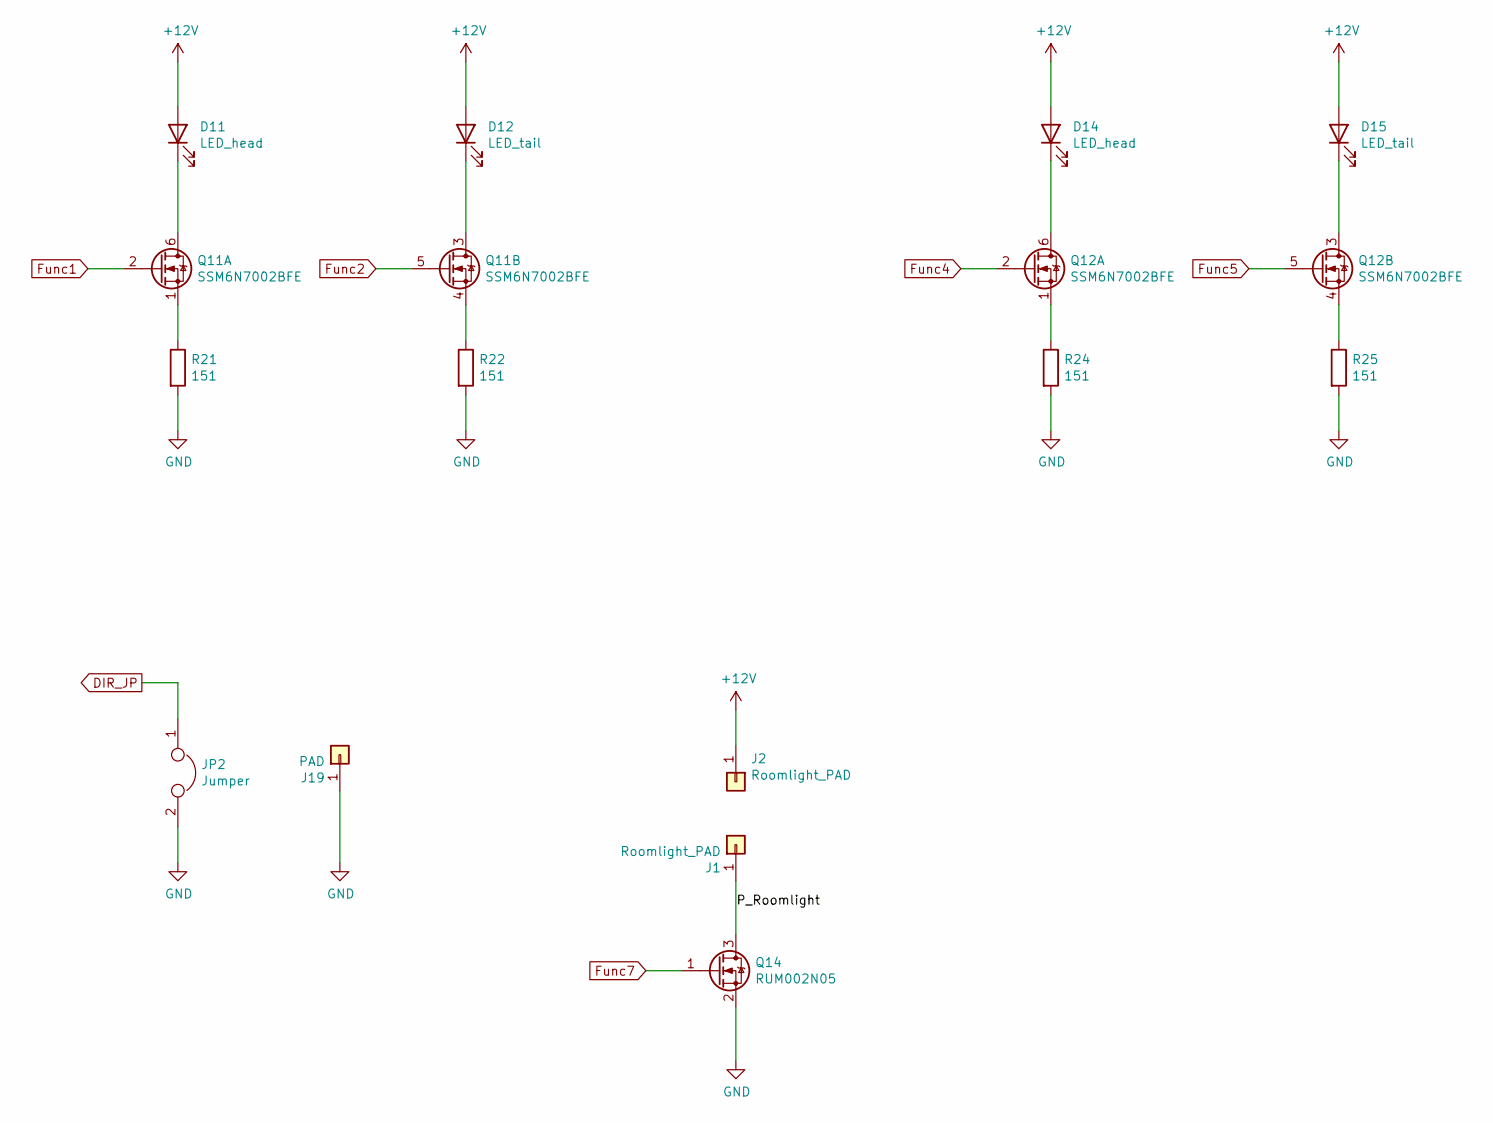
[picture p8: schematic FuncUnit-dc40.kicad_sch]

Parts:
D11, D14: LED_head; LED_1608_SLIMPAD
D12, D15: LED_tail; LED_1608_SLIMPAD
J1, J2: Roomlight_PAD; PAD_1.0x1.8_SMD
J19: PAD; PAD_0.6x1.0_SMD
JP2: Jumper; SOLDER_CONN_PAD_2_1.5mm
Q11, Q12: SSM6N7002BFE; SOT-666-nomark-v2
Q14: RUM002N05; SOT-723
R21, R22, R24, R25: 151; R_1608_20240411

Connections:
+12V: D11.2 (A), D12.2 (A), D14.2 (A), D15.2 (A), J2.1; also elsewhere on the board
/FuncUnit-dc40/P_Roomlight: J1.1, Q14.3 (D)
DIR_JP: JP2.1; also elsewhere on the board
Func1: Q11.2 (G); also elsewhere on the board
Func2: Q11.5 (G); also elsewhere on the board
Func4: Q12.2 (G); also elsewhere on the board
Func5: Q12.5 (G); also elsewhere on the board
Func7: Q14.1 (G); also elsewhere on the board
GND: J19.1, JP2.2, Q14.2 (S), R21.2, R22.2, R24.2, R25.2; also elsewhere on the board
unnamed: D11.1 (K), Q11.6 (D)
unnamed: D12.1 (K), Q11.3 (D)
unnamed: D14.1 (K), Q12.6 (D)
unnamed: D15.1 (K), Q12.3 (D)
unnamed: Q11.1 (S), R21.1
unnamed: Q11.4 (S), R22.1
unnamed: Q12.1 (S), R24.1
unnamed: Q12.4 (S), R25.1

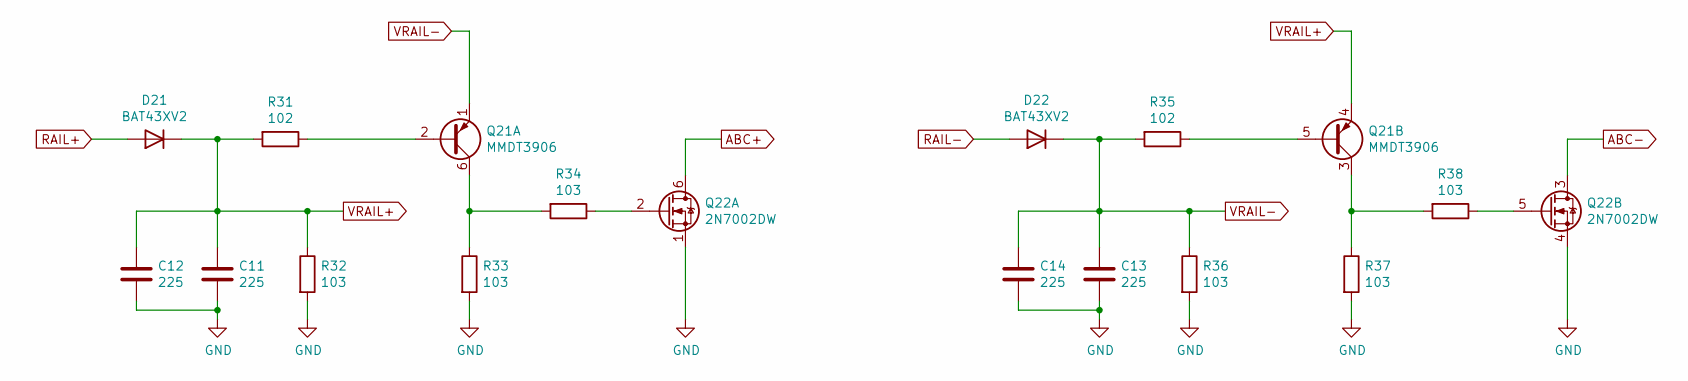
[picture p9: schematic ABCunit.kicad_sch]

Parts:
C11, C12, C13, C14: 225; C_1005_v4
D21, D22: BAT43XV2; SOD-523
Q21: MMDT3906; SOT-666-nomark-v2
Q22: 2N7002DW; SOT-666-nomark-v2
R31, R35: 102; R_1005_20240411
R32, R33, R34, R36, R37, R38: 103; R_1005_20240411

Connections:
ABC+: Q22.6 (D); also elsewhere on the board
ABC-: Q22.3 (D); also elsewhere on the board
GND: C11.2, C12.2, C13.2, C14.2, Q22.1 (S), Q22.4 (S), R32.2, R33.2, R36.2, R37.2; also elsewhere on the board
unnamed: Q21.2 (B1), R31.1
unnamed: Q21.6 (C1), R33.1, R34.2
unnamed: Q21.5 (B2), R35.1
unnamed: Q21.3 (C2), R37.1, R38.2
unnamed: Q22.2 (G), R34.1
unnamed: Q22.5 (G), R38.1
RAIL+: D21.2 (A); also elsewhere on the board
RAIL-: D22.2 (A); also elsewhere on the board
VRAIL+: C11.1, C12.1, D21.1 (K), Q21.4 (E2), R31.2, R32.1
VRAIL-: C13.1, C14.1, D22.1 (K), Q21.1 (E1), R35.2, R36.1

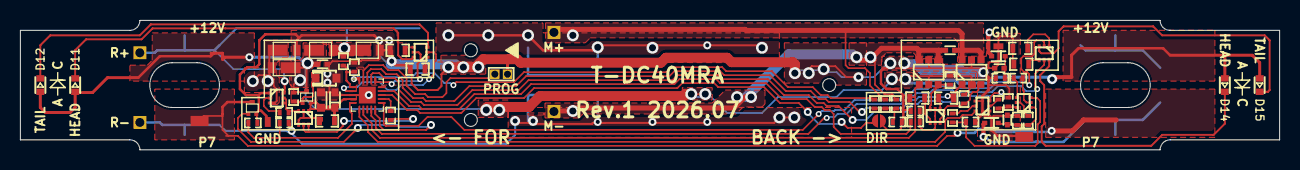
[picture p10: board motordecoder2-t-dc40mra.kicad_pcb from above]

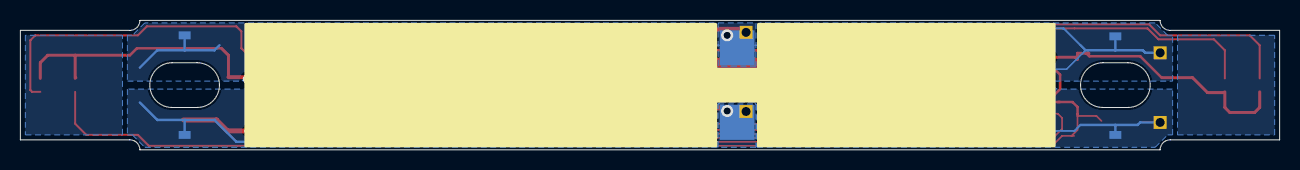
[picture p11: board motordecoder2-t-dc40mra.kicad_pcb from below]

Board: 2 copper layers, 126.5 x 13.0 mm, 80 parts (6 on the bottom side), 51 nets.

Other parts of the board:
H3#2: 1.3mm; Hole_1.3mm

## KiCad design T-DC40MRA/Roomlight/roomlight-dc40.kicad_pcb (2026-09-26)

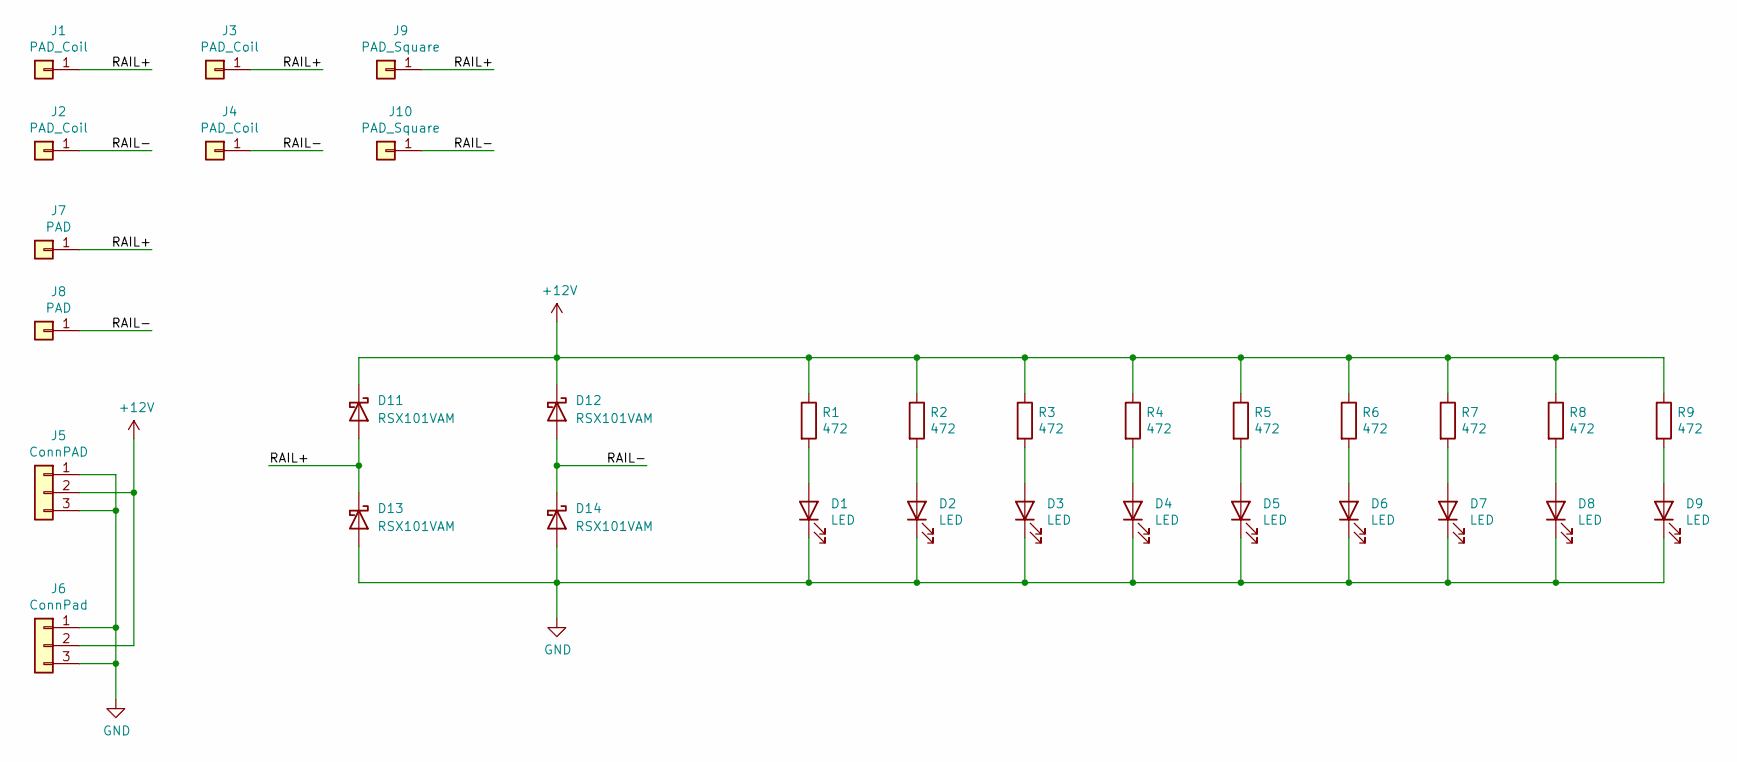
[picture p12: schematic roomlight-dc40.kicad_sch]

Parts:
D1, D2, D3, D4, D5, D6, D7, D8, D9: LED; LED_1608_SLIMPAD
D11, D12, D13, D14: RSX101VAM; TUMD2M
J1, J2, J3, J4: PAD_Coil; PAD_COIL_1.3x1.3_NoHole
J5: ConnPAD; PCB_CONN_PAD_3pin_2.5mmx1.2mm_SMD
J6: ConnPad; PCB_CONN_PAD_3pin_2.5mmx1.2mm_SMD
J7, J8: PAD; PAD_1.0x1.8_SMD
J9, J10: PAD_Square; PAD_Square_1.3x1.3_Hole0.8
R1, R2, R3, R4, R5, R6, R7, R8, R9: 472; R_1608_20240411

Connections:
+12V: D11.1 (K), D12.1 (K), J5.2, J6.2, R1.1, R2.1, R3.1, R4.1, R5.1, R6.1, R7.1, R8.1, R9.1
/RAIL+: D11.2 (A), D13.1 (K), J1.1, J3.1, J7.1, J9.1
/RAIL-: D12.2 (A), D14.1 (K), J2.1, J4.1, J8.1, J10.1
GND: D1.1 (K), D2.1 (K), D3.1 (K), D4.1 (K), D5.1 (K), D6.1 (K), D7.1 (K), D8.1 (K), D9.1 (K), D13.2 (A), D14.2 (A), J5.1, J5.3, J6.1, J6.3
unnamed: D1.2 (A), R1.2
unnamed: D2.2 (A), R2.2
unnamed: D3.2 (A), R3.2
unnamed: D4.2 (A), R4.2
unnamed: D5.2 (A), R5.2
unnamed: D6.2 (A), R6.2
unnamed: D7.2 (A), R7.2
unnamed: D8.2 (A), R8.2
unnamed: D9.2 (A), R9.2

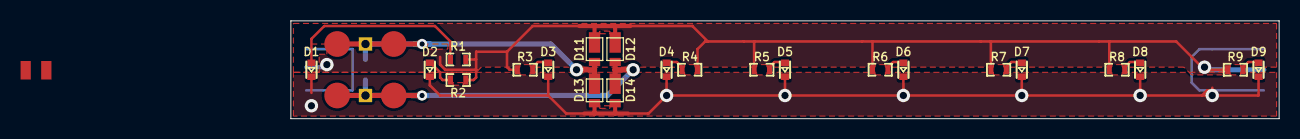
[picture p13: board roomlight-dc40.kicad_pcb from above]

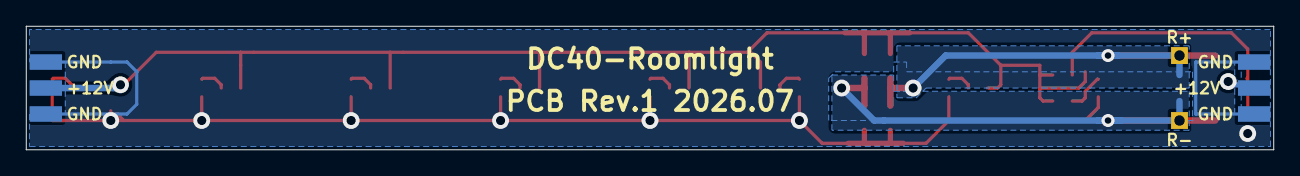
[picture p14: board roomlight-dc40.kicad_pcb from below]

Board: 2 copper layers, 96.0 x 9.5 mm, 32 parts (2 on the bottom side), 13 nets.

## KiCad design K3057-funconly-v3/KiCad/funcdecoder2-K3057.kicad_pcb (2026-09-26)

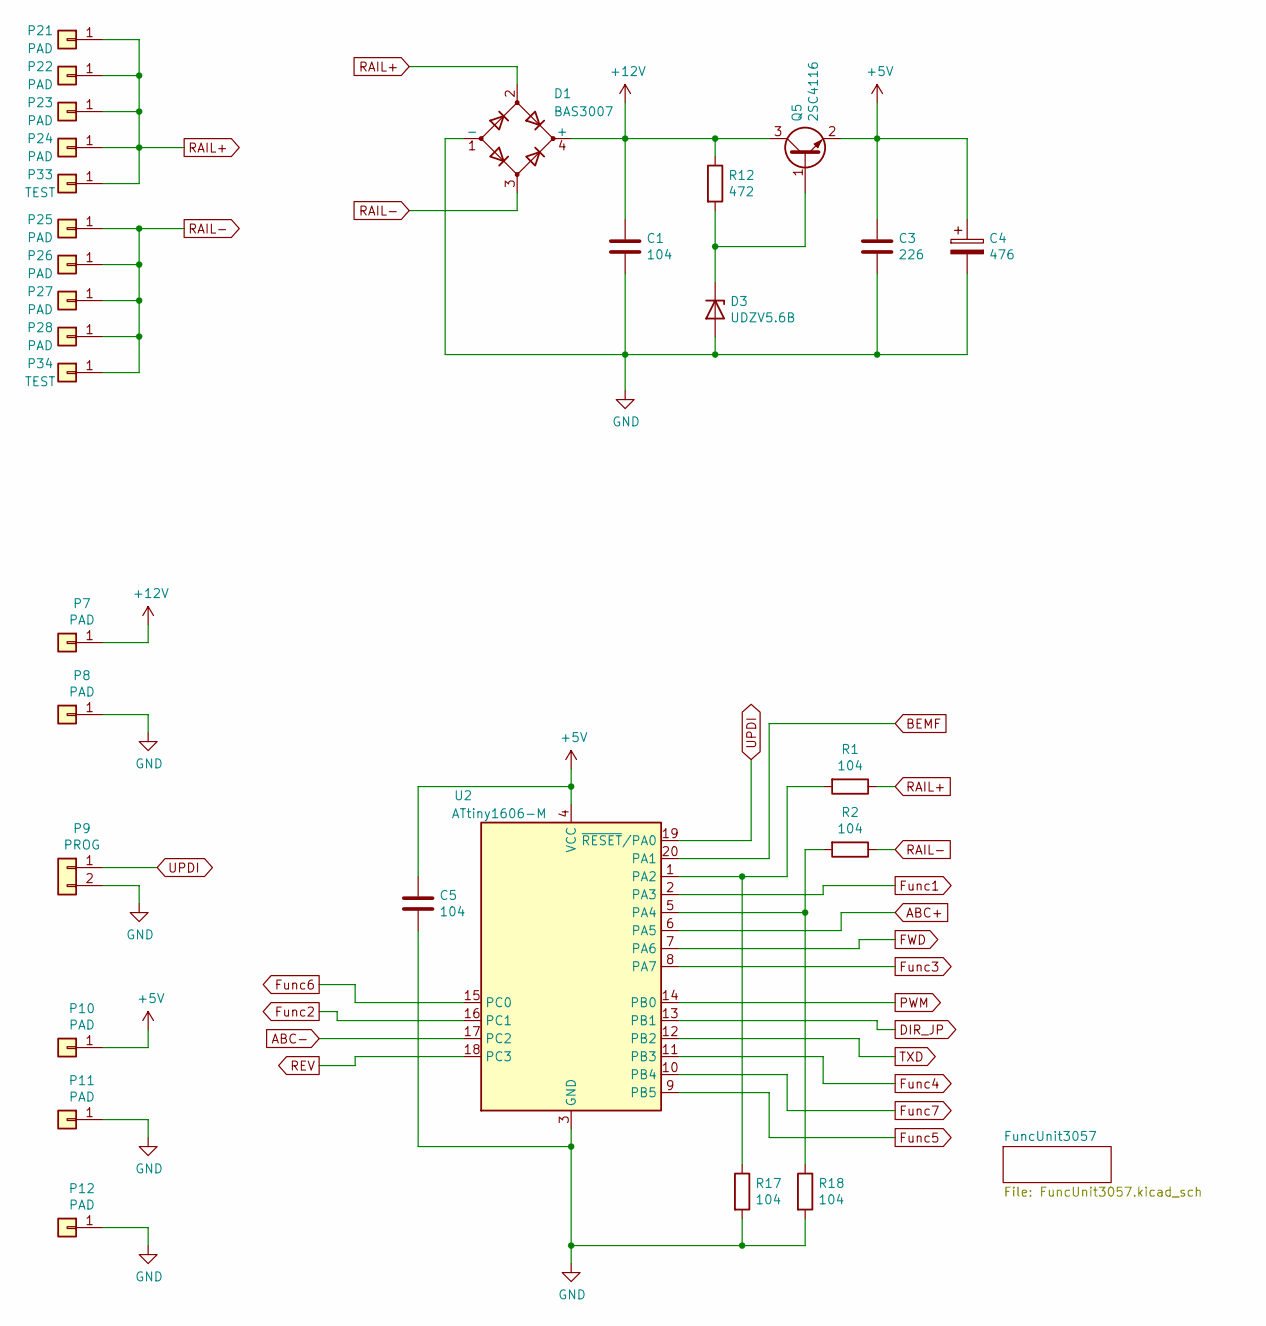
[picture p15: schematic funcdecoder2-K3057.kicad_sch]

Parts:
C1, C5: 104; C_1005_v4
C3: 226; C_1608_v4
C4: 476; CP_1608
D1: BAS3007; SOT-143
D3: UDZV5.6B; UMD2
P7: PAD; PAD_1.0x1.8_SMD
P8, P10: PAD; PAD_0.6x1.0_SMD
P9: PROG; PAD_PROG_2PIN_HOLE0.7
P11: PAD; PAD_0.5x1.2_SMD
P12: PAD; PAD_1.0x1.4_SMD
P21, P24, P25, P28: PAD; KATO_RAILPAD_3057_8mm
P22, P23, P26, P27: PAD; KATO_RAILPAD_3057_7mm
P33, P34: TEST; PAD_1.2x1.2_Hole0.7
Q5: 2SC4116; SC-70_v2
R1, R2, R17, R18: 104; R_1608_20240411
R12: 472; R_1608_20240411
U2: ATtiny1606-M; VQFN-20-1EP_3x3mm_P0.4mm_EP1.7x1.7mm

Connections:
+5V: C3.1, C4.1, C5.1, P10.1, Q5.2 (E), U2.4 (VCC)
+12V: C1.1, D1.4 (+), P7.1, Q5.3 (C), R12.1; also elsewhere on the board
ABC+: U2.6 (PA5)
ABC-: U2.17 (PC2)
BEMF: U2.20 (PA1)
DIR_JP: U2.13 (PB1); also elsewhere on the board
FWD: U2.7 (PA6)
Func1: U2.2 (PA3); also elsewhere on the board
Func2: U2.16 (PC1); also elsewhere on the board
Func3: U2.8 (PA7); also elsewhere on the board
Func4: U2.11 (PB3); also elsewhere on the board
Func5: U2.9 (PB5); also elsewhere on the board
Func6: U2.15 (PC0); also elsewhere on the board
Func7: U2.10 (PB4); also elsewhere on the board
GND: C1.2, C3.2, C4.2, C5.2, D1.1 (-), D3.2 (A), P8.1, P9.2, P11.1, P12.1, R17.2, R18.2, U2.3 (GND), U2.21 (GND); also elsewhere on the board
unnamed: D3.1 (K), Q5.1 (B), R12.2
unnamed: R1.2, R17.1, U2.1 (PA2)
unnamed: R2.2, R18.1, U2.5 (PA4)
PWM: U2.14 (PB0)
RAIL+: D1.2, P21.1, P22.1, P23.1, P24.1, P33.1, R1.1
RAIL-: D1.3, P25.1, P26.1, P27.1, P28.1, P34.1, R2.1
REV: U2.18 (PC3)
TXD: U2.12 (PB2)
UPDI: P9.1, U2.19 (~RESET/PA0)

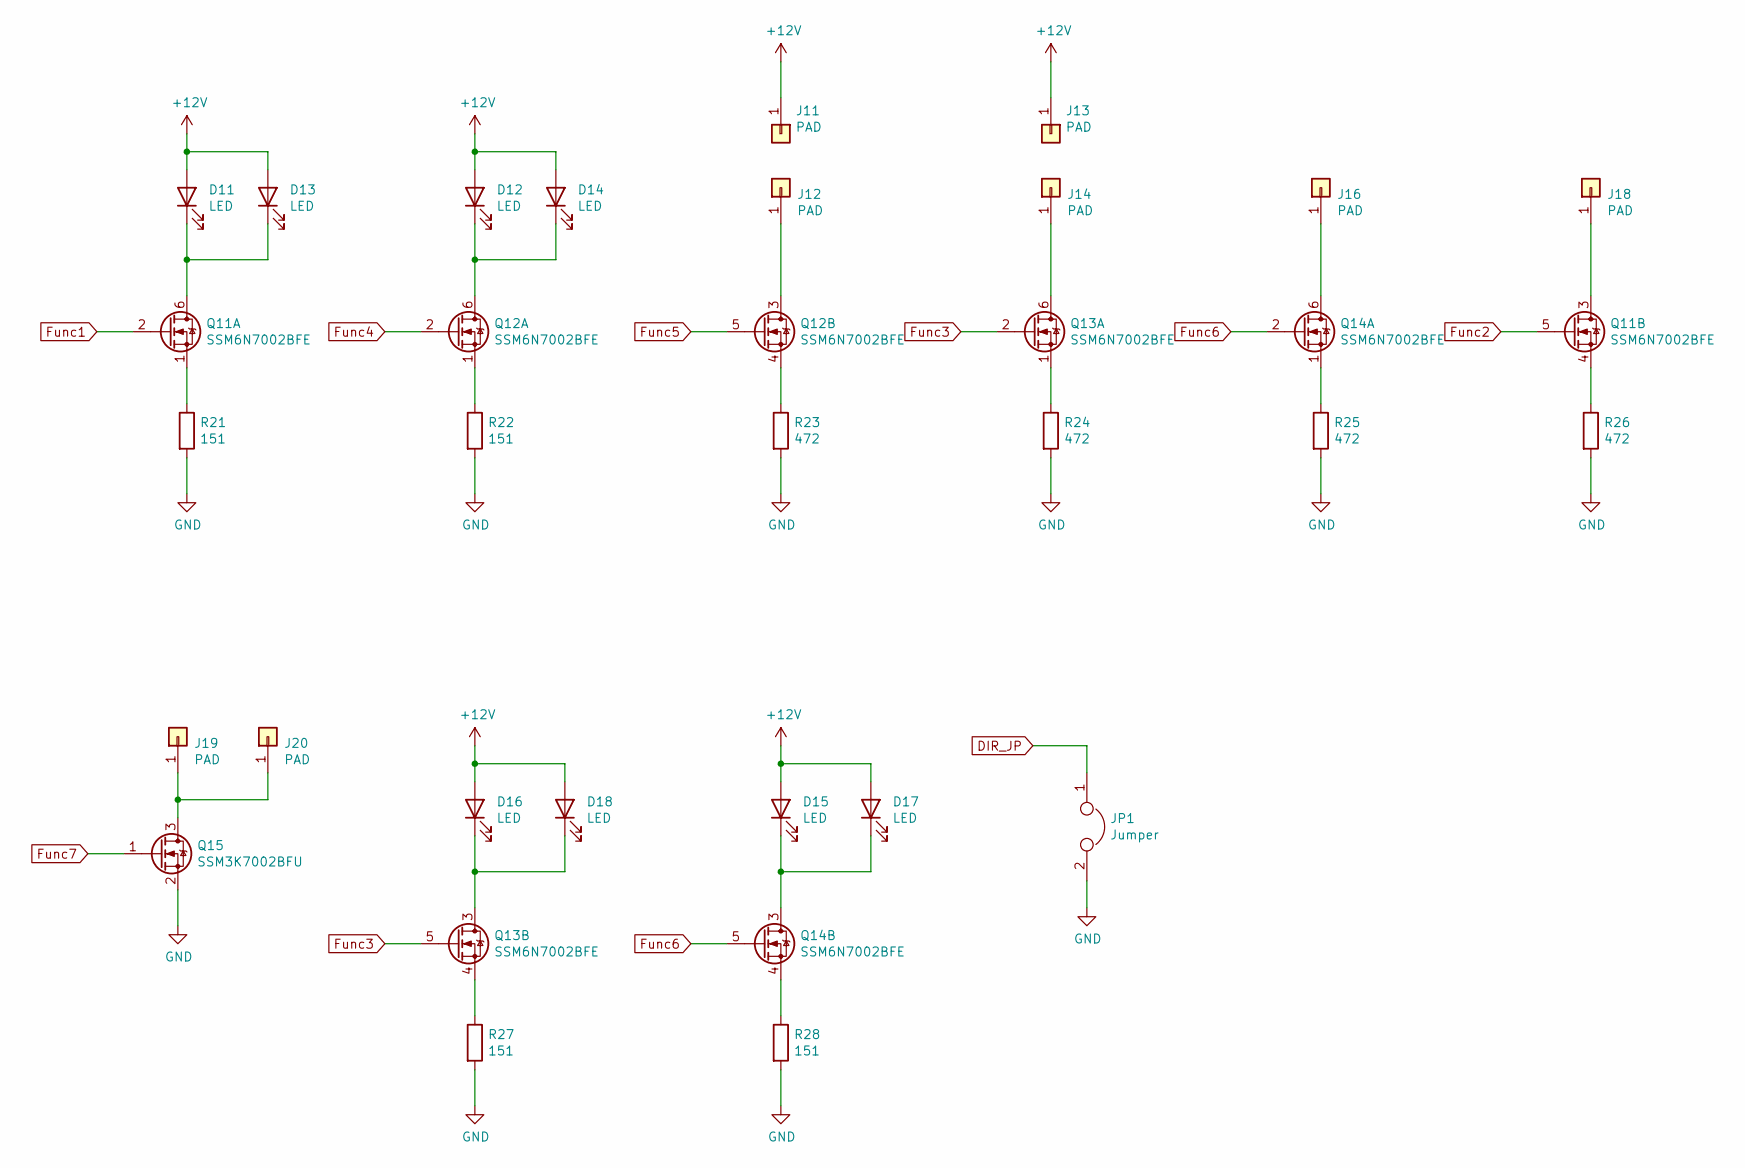
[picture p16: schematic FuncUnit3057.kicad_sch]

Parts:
D11, D12, D13, D14, D15, D16, D17, D18: LED; LED_1224_1005_SIDE_BIG2
J11, J13: PAD; PAD_1.0x1.8_SMD
J12, J14, J16, J18: PAD; PAD_1.0x1.0_Hole0.6
J19: PAD; PAD_1.0x1.4_SMD
J20: PAD; PAD_0.5x1.2_SMD
JP1: Jumper; SOLDER_CONN_PAD_2_1.5mm
Q11, Q12, Q13, Q14: SSM6N7002BFE; SOT-666-nomark-v2
Q15: SSM3K7002BFU; SC-70_v2
R21, R22, R27, R28: 151; R_1608_20240411
R23, R25: 472; R_1005_20240411
R24, R26: 472; R_1608_20240411

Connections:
+12V: D11.2 (A), D12.2 (A), D13.2 (A), D14.2 (A), D15.2 (A), D16.2 (A), D17.2 (A), D18.2 (A), J11.1, J13.1; also elsewhere on the board
DIR_JP: JP1.1; also elsewhere on the board
Func1: Q11.2 (G); also elsewhere on the board
Func2: Q11.5 (G); also elsewhere on the board
Func3: Q13.2 (G), Q13.5 (G); also elsewhere on the board
Func4: Q12.2 (G); also elsewhere on the board
Func5: Q12.5 (G); also elsewhere on the board
Func6: Q14.2 (G), Q14.5 (G); also elsewhere on the board
Func7: Q15.1 (G); also elsewhere on the board
GND: JP1.2, Q15.2 (S), R21.2, R22.2, R23.2, R24.2, R25.2, R26.2, R27.2, R28.2; also elsewhere on the board
unnamed: D11.1 (K), D13.1 (K), Q11.6 (D)
unnamed: D12.1 (K), D14.1 (K), Q12.6 (D)
unnamed: D15.1 (K), D17.1 (K), Q14.3 (D)
unnamed: D16.1 (K), D18.1 (K), Q13.3 (D)
unnamed: J12.1, Q12.3 (D)
unnamed: J14.1, Q13.6 (D)
unnamed: J16.1, Q14.6 (D)
unnamed: J18.1, Q11.3 (D)
unnamed: J19.1, J20.1, Q15.3 (D)
unnamed: Q11.1 (S), R21.1
unnamed: Q11.4 (S), R26.1
unnamed: Q12.1 (S), R22.1
unnamed: Q12.4 (S), R23.1
unnamed: Q13.1 (S), R24.1
unnamed: Q13.4 (S), R27.1
unnamed: Q14.1 (S), R25.1
unnamed: Q14.4 (S), R28.1

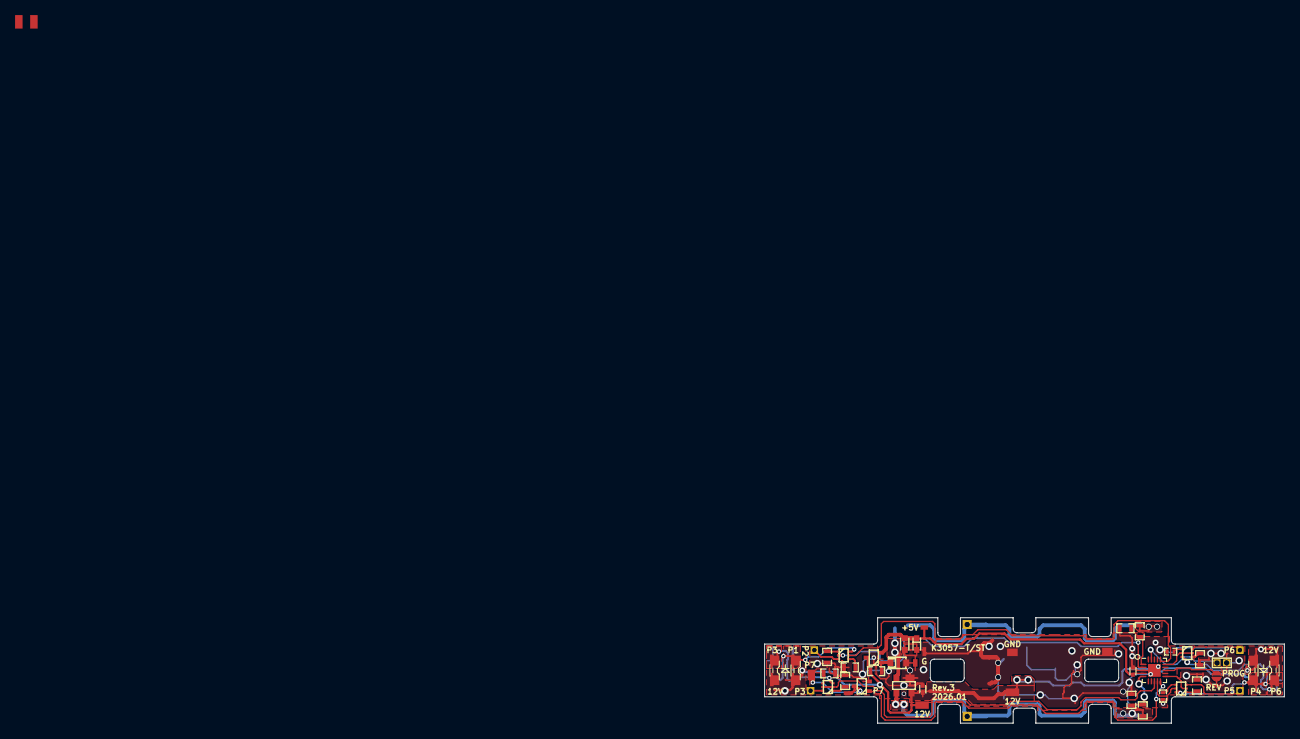
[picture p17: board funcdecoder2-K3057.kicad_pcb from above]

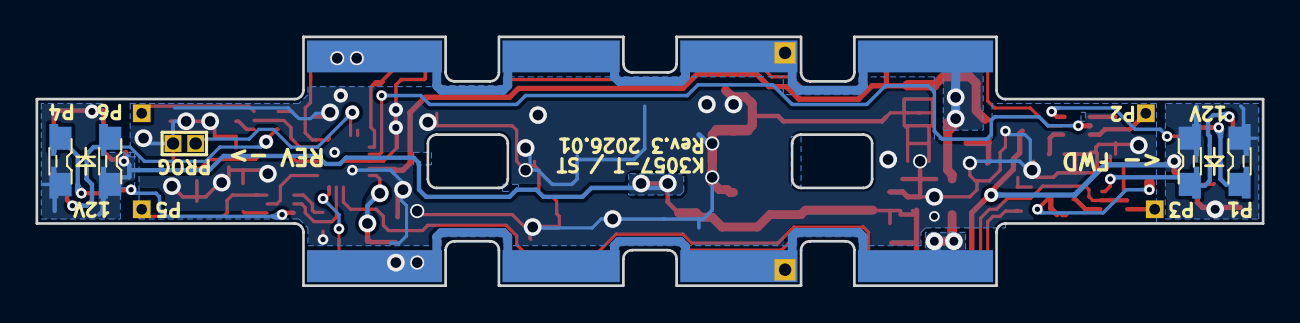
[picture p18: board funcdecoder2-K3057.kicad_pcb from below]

Board: 2 copper layers, 69.0 x 14.0 mm, 61 parts (4 on the bottom side), 34 nets.

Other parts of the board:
P7#2: PAD; PAD_1.0x1.8_SMD
P12#2: PAD; PAD_1.0x1.4_SMD

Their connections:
+12V: P7#2.1; also elsewhere on the board
GND: P12#2.1; also elsewhere on the board

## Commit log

2021-04-24 回路の問題点を修正 (K3066: Rev3 / それ以外: Rev2)
    [FuncUnit3057.sch, FuncUnit3066.sch, FuncUnitRoomlight.sch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]
2021-04-24 v2021-04へのリンクを追加
2021-05-14 基板上のF表記をP表記に変更
    [motordecoder2-K3057.kicad_pcb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]
2021-05-14 記載内容を2021.05版に修正
2021-05-14 汎用デコーダの設計データを追加
    [ABCunit.sch, FuncUnitNormal.sch, motordecoder2_normal.kicad_pcb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]
2021-05-14 面付けデータのリンクを削除 (未作成のため)
2021-05-14 画像ファイル名間違いを修正
2022-03-10 (K3057RA) 表面のLEDパッドを増設
    [ABCunit.sch, FuncUnit3057.sch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]
2022-03-10 (K3066RA v2) 形状を変更したバージョンを追加
    [ABCunit.sch, FuncUnit3066.sch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]
2024-09-18 gitignoreを更新
2024-09-18 K3066RA v3の設計データを追加
    [ABCunit.kicad_sch, FuncUnit3066.kicad_sch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]
2024-09-18 K3057RA v2の設計データを追加
    [ABCunit.kicad_sch, ABCunit.sch, FuncUnit3057.kicad_sch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]
2024-09-18 K7012RAの設計データを追加
    [ABCunit.sch, K7012RA.kicad_pcb, K7012RA.sch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]
2024-09-18 gitignoreを修正
2024-09-18 ファンクション専用デコーダの設計データを追加
    [F02-Func-Decoder-p.GBL, F02-Func-Decoder-p.GBO, F02-Func-Decoder-p.GBP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]
